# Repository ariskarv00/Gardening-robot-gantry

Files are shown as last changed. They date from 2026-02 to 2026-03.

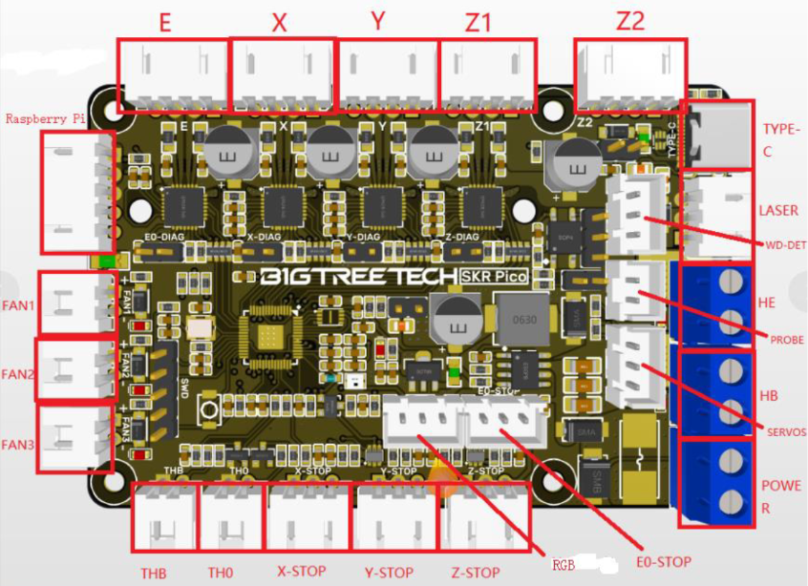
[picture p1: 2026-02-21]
electronics/SKR pico schematics.png

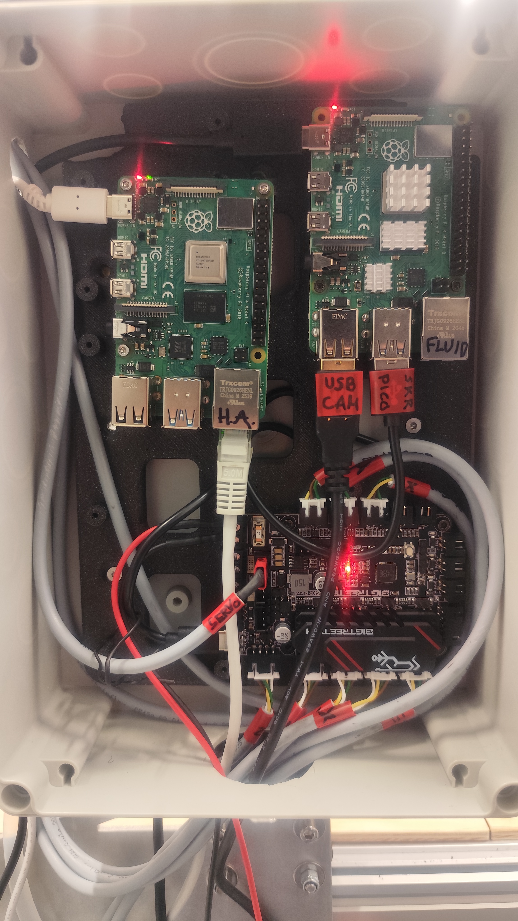
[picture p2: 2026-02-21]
electronics/IMG_20260129_140712.jpg

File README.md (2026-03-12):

# Gardening Robot Gantry (Danish Technical University - Skylab)

Modular Cartesian gardening robot inspired by the FarmBot Genesis, designed and built at DTU Skylab as a platform for student projects, course integration, and future startup exploration.

DTU Skylab - Gardening Robot - Demonstration: https://studio.youtube.com/video/Ki-VsF5vse0/edit

DTU Skylab - Gardening Robot - Seeding Sequence Testing: https://www.youtube.com/watch?v=myrVL9h8MHA 

DTU Skylab - Gardening Robot - Basic movements demo: https://www.youtube.com/watch?v=C3N4Af2INCI

Farmbot: https://farm.bot/

Farmbot Genesis Documentation: https://genesis.farm.bot/v1.8/assembly/intro

\## Features

\- 4×4 modular pot grid with laser‑cut wooden puzzle frame and 3D‑printed connectors  

\- Aluminum‑extrusion CNC gantry with V‑slot X/Z and leadscrew Y‑axis  

\- Toolhead with seed dispenser, watering nozzle, peristaltic pump, and USB camera  

\- Fully automated sequence: drill hole → drop seed → cover → water  

\- Calibrated peristaltic pump with ml‑per‑mm factor  

\- Browser‑based control via Klipper + Fluidd and automation via Home Assistant  

\## Repository layout

\- `hardware/` – CAD models (.f3d), .DXF for wooden puzzle grid, and BOM (.xlsx) 

\- `electronics/` – Schematics and wiring diagrams, pictures of connections 

\- `firmware/klipper/` – `printer.cfg` and pictures of Fluidd UI 

\- `documentation/` – Build guide, user guide, and notes for future improvements  

\- `pictures/` – Pictures of the assembly and 3D models

\## Hardware overview

\- Aluminum extrusion frame and V‑slot linear motion  

\- Custom metal parts (milled, lathed, laser‑/waterjet‑cut, hand‑finished)  

\- Laser‑cut 16‑pot grid mounted on 3D‑printed legs and extrusion supports  

\- NEMA17 steppers, micro servo for seed dispenser, peristaltic pump, mechanical endstops  

\## Electronics \& software

\- 1× Raspberry Pi running Klipper + Fluidd with BTT SKR Pico motion controller  

\- 1× Raspberry Pi running Home Assistant for automation  

\- Custom wiring with JST connectors and soldered harnesses  

\- Klipper configuration for axis calibration, safe homing, travel limits, and planting/watering macros  

\## Documentation

See `documentation/` for:

\- Step‑by‑step build instructions - Also follow Farmbot's Genesis documentation: https://genesis.farm.bot/v1.8/assembly/intro

\- Basic operation and maintenance  

\- Ideas and guidelines for future extensions (vision, sensors, new tools)

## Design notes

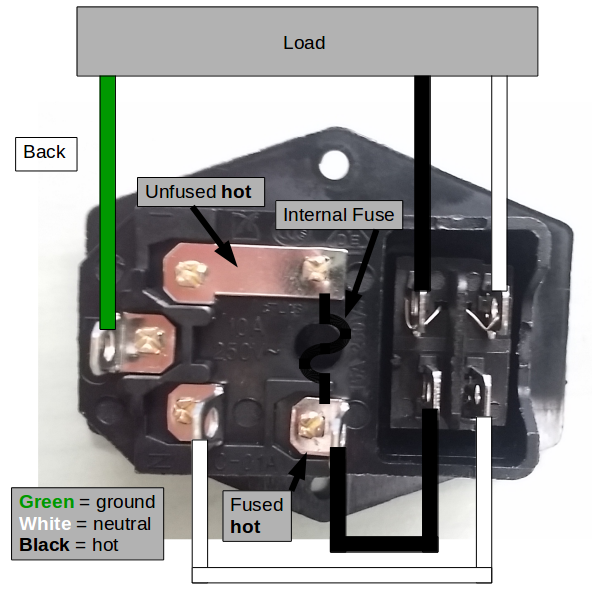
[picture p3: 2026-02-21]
electronics/IEC switch connection.webp

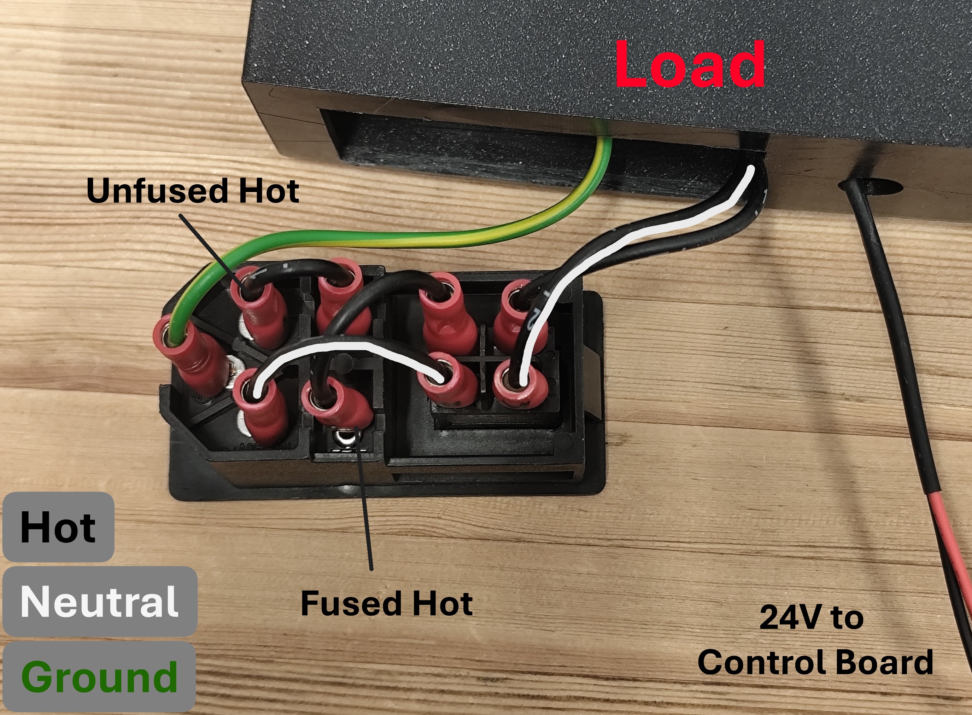
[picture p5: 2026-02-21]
electronics/Fuse Switch.jpg

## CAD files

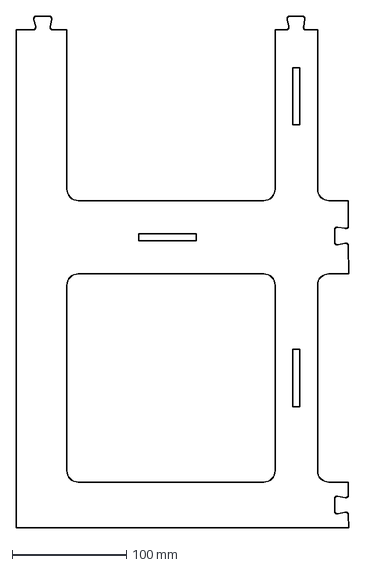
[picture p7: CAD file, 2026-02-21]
hardware/DXF Files for Wooden Puzzle-Grid/3.dxf
290.1 x 447.1 mm

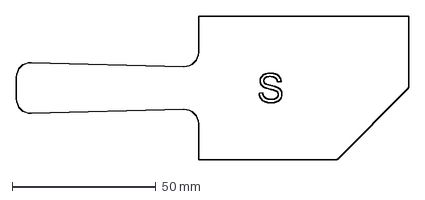
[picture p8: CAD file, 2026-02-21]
hardware/DXF Files for Wooden Puzzle-Grid/Short 2.dxf
136.3 x 50.0 mm

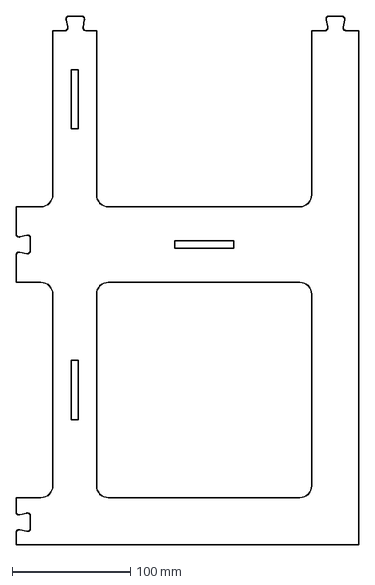
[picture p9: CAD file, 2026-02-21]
hardware/DXF Files for Wooden Puzzle-Grid/1.dxf
290.1 x 447.2 mm

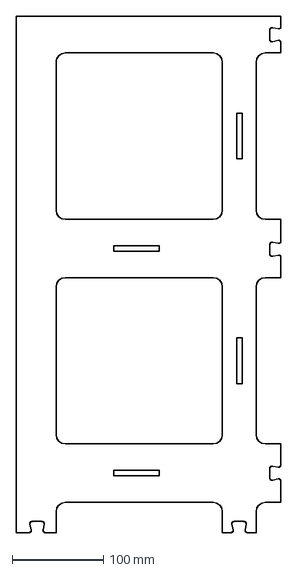
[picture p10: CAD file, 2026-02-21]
hardware/DXF Files for Wooden Puzzle-Grid/6.dxf
290.1 x 565.0 mm

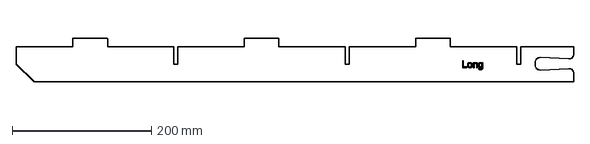
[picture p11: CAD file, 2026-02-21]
hardware/DXF Files for Wooden Puzzle-Grid/Long 1.dxf
800.0 x 62.0 mm

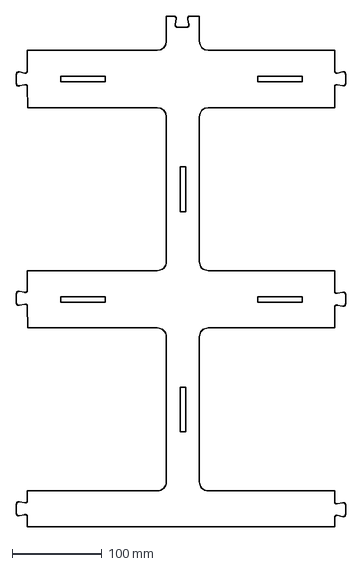
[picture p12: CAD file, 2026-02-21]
hardware/DXF Files for Wooden Puzzle-Grid/2.dxf
367.4 x 570.0 mm

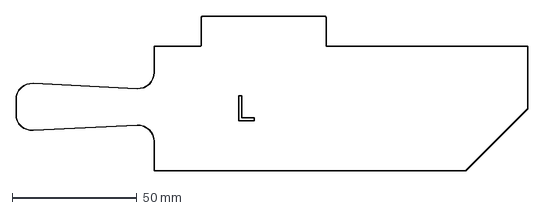
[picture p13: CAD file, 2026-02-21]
hardware/DXF Files for Wooden Puzzle-Grid/Long 2.dxf
205.4 x 62.0 mm

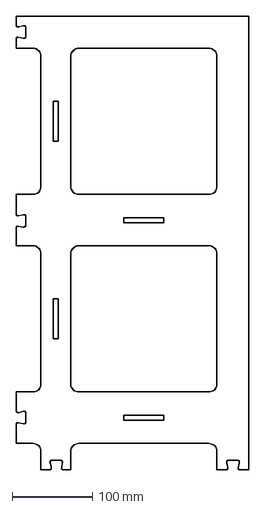
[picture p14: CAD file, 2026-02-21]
hardware/DXF Files for Wooden Puzzle-Grid/4.dxf
290.1 x 565.0 mm

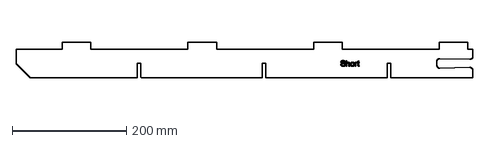
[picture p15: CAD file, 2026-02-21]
hardware/DXF Files for Wooden Puzzle-Grid/Short 1.dxf
800.0 x 62.0 mm

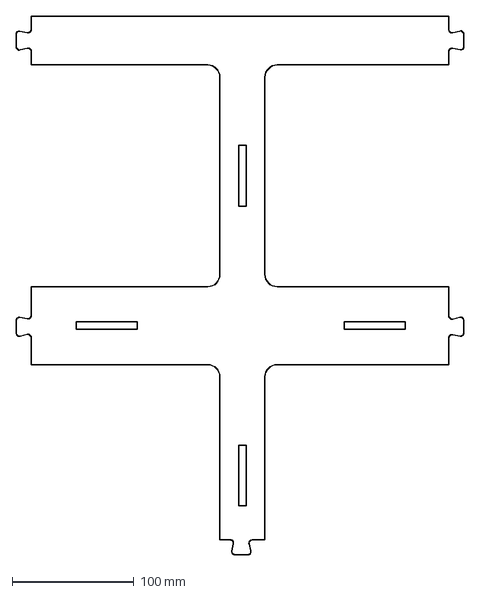
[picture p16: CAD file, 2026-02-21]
hardware/DXF Files for Wooden Puzzle-Grid/5.dxf
367.2 x 442.1 mm

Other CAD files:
hardware/Parametric Cable Chain.f3d
hardware/Parametric Peristaltic Pump with Mount.f3d

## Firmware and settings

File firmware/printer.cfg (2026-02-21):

[include fluidd.cfg]
[mcu]
 serial: /dev/serial/by-id/usb-Klipper_rp2040_45503571290C9388-if00

[virtual_sdcard]
path: /home/pi/printer_data/gcodes
on_error_gcode: CANCEL_PRINT

[printer]
kinematics: cartesian
max_velocity: 85    ;max velocity 85 for Z-axis not to malfuction
max_accel: 400
max_z_velocity: 80
max_z_accel: 400

[homing_override]
axes: yxz
gcode:
    G28 Y # Y axis first for safety (vertical)
    G28 X # home X axis
    G28 Z # home Z axis
    
[gcode_arcs]
resolution: 1.0
#   An arc will be split into segments. Each segment's length will
#   equal the resolution in mm set above. Lower values will produce a
#   finer arc, but also more work for your machine. Arcs smaller than
#   the configured value will become straight lines. The default is
#   1mm.

[stepper_x]
step_pin: gpio11
dir_pin: !gpio10
enable_pin: !gpio12
microsteps: 16
rotation_distance: 20   # CALIBRATION FORMULA: RD'=RD*(Lmeasured/Lreal),  
endstop_pin: !gpio4        # Lmeasured= the 'wrong' one, Lreal= real measured
position_endstop: 0
position_max: 730
homing_speed: 65
second_homing_speed: 10

[tmc2209 stepper_x]
uart_pin: gpio9
tx_pin: gpio8
uart_address: 0
run_current: 0.8
hold_current: 0.6
stealthchop_threshold: 999999

[stepper_y]
step_pin: gpio6
dir_pin: !gpio5
enable_pin: !gpio7
microsteps: 16
rotation_distance: 3.8
endstop_pin: !gpio3
position_endstop: 0
position_max: 315  
homing_speed: 35  
second_homing_speed: 10 


[tmc2209 stepper_y]
uart_pin: gpio9
tx_pin: gpio8
uart_address: 2
run_current: 0.8
hold_current: 0.6
stealthchop_threshold: 999999
diag_pin: ^gpio3
driver_SGTHRS: 100

[stepper_z]
step_pin: gpio19
dir_pin: gpio28
enable_pin: !gpio2
microsteps: 16
rotation_distance: 20
endstop_pin: !gpio25
position_endstop: 0
position_min: -2.0
position_max: 730
homing_speed: 55
second_homing_speed: 10
homing_retract_dist: 5.0


[tmc2209 stepper_z]
uart_pin: gpio9
tx_pin: gpio8
uart_address: 1
run_current: 1.2
hold_current: 0.6
stealthchop_threshold: 999999

[extruder]
step_pin: gpio14
dir_pin: !gpio13
enable_pin: !gpio15
microsteps: 16
rotation_distance: 14 ;So that mm translates into mL
nozzle_diameter: 0.4
filament_diameter: 1.75
heater_pin: gpio23
sensor_type: EPCOS 100K B57560G104F
sensor_pin: gpio27
control: pid
pid_Kp: 22.2
pid_Ki: 1.08
pid_Kd: 114
min_temp: -25 
max_temp: 20
max_extrude_cross_section:2
min_extrude_temp:-25
max_extrude_only_distance: 50000.0   ; or some value larger than the longest pump cycle you expect
max_extrude_cross_section: 10000.0      ; or even higher if you need greater flow
max_extrude_only_velocity: 600.0    # mm/s  — start conservative for a pump
max_extrude_only_accel: 2000.0    # mm/s^2 — reasonable starting accel

[tmc2209 extruder]
uart_pin: gpio9
tx_pin: gpio8
uart_address: 3
run_current: 1.00
hold_current: 0.800
stealthchop_threshold: 0

[gcode_macro MOVE_TO_PUMP_CALIBRATION_POSITION_B2]
description: Go to position and down to calibrate pump
gcode:
    G90
    G0 Y0 F4000
    G0 X287 Z230 F9999
    G0 Y300 F4000

[gcode_macro WATER_PLANT_CENTER]
description: Dispense water using peristaltic pump (slow start)
gcode:
    {% set volume = params.VOLUME|default(100)|float %}
    {% set flow_rate = params.FLOW_RATE|default(2000)|float %}

    ; CALIBRATION: mm of E per ml
    {% set e_per_ml = 4.1 %}
    {% set e_total = volume * e_per_ml %}

    {% set e_start = 10.0 %}
    {% set e_start = e_start if e_start < e_total else e_total %}
    {% set e_rest = e_total - e_start %}

    M83                     ; Relative extruder mode

    ; Slow start (anti-stall)
    G1 E{e_start} F500

    ; Normal watering
    {% if e_rest > 0 %}
        G1 E{e_rest} F{flow_rate}
    {% endif %}

    G4 P1000                ; Let flow finish
    M82                     ; Absolute extruder mode


[gcode_macro WATER_AFTER_PLANTING]
description: Water seed after planting with slow start then fast flow
gcode:
    ; --- Move nozzle to watering height ---
    G90
    G0 Y200 F4000

    ; --- Slow priming phase (5 ml at low speed) ---
    {% set slow_volume = 5 %}
    {% set slow_flow = 500 %}
    {% set slow_e = slow_volume * 2 %}   ; CALIBRATED: mm per ml

    M83
    G1 E{slow_e} F{slow_flow}
    G4 P500

    ; --- Main watering phase (55 ml at high speed) ---
    {% set fast_volume = 55 %}
    {% set fast_flow = 3000 %}
    {% set fast_e = fast_volume * 2 %}

    G1 E{fast_e} F{fast_flow}
    G4 P1000
    M82


[servo Seeder]
pin: gpio29          # g-code command  SET_SERVO SERVO=Seeder ANGLE=180
maximum_servo_angle: 180
#   The maximum angle (in degrees) that this servo can be set to. The
#   default is 180 degrees.
#initial_angle:
#   Initial angle (in degrees) to set the servo to. The default is to
#   not send any signal at startup.

[gcode_macro DROP_SEED]
description: Drop seed at current position 
gcode:
    G4 P500  
      SET_SERVO SERVO=Seeder ANGLE=180  ; Rotate to release seed
      G4 P500                    ; Brief pause for seed to drop
      SET_SERVO SERVO=Seeder ANGLE=0    ; Return to closed position
    G4 P500  


[gcode_macro DROP_SEED_WITH_VIBRATION]
description: Drop seed at current position with vibration to free stuck pellets
gcode:
    # Small delay before starting
    G4 P500  

    ################################################################
    # 1) PRE-DROP VIBRATION AROUND CLOSED POSITION (0°)
    ################################################################
    
    SET_SERVO SERVO=Seeder ANGLE=70
    G4 P100                    ; Brief pause
    SET_SERVO SERVO=Seeder ANGLE=0
    G4 P100                    ; Brief pause
    SET_SERVO SERVO=Seeder ANGLE=70
    G4 P100                    ; Brief pause
    SET_SERVO SERVO=Seeder ANGLE=0
    G4 P100                    ; Brief pause
    SET_SERVO SERVO=Seeder ANGLE=70
    G4 P100                    ; Brief pause
    SET_SERVO SERVO=Seeder ANGLE=0
    G4 P100                    ; Brief pause
    SET_SERVO SERVO=Seeder ANGLE=70
    G4 P100                    ; Brief pause
    SET_SERVO SERVO=Seeder ANGLE=0
    G4 P50                    ; Brief pause
    SET_SERVO SERVO=Seeder ANGLE=70
    G4 P100                    ; Brief pause
    SET_SERVO SERVO=Seeder ANGLE=0
    G4 P100                    ; Brief pause
    SET_SERVO SERVO=Seeder ANGLE=70
    G4 P100                    ; Brief pause
    SET_SERVO SERVO=Seeder ANGLE=0
    G4 P100                    ; Brief pause

    SET_SERVO SERVO=Seeder ANGLE=180      ; Rotate to release seed
    

    G4 P800    ; brief pause for seed to drop

    SET_SERVO SERVO=Seeder ANGLE=0    ; Return to closed position


    G4 P500    ; end delay

[gcode_macro PLANT_SEED_WITH_HOLE_FIRST]
description: Plant seed at current position, making a hole first
gcode:
    G91
    G0 X10 F4000               ; Move X above the hole
    G90

    G0 Y312 F9999              ; Move down to make a hole
    G0 Y285 F4000              ; Move up begin seed drop sequence
    
    G91                        ; 
    G0 X-10 F4000               ; Move X above the hole
    G90
    
    G4 P500  
    SET_SERVO SERVO=Seeder ANGLE=180  ; Rotate to release seed
    G4 P500                           ; Brief pause for seed to drop
    SET_SERVO SERVO=Seeder ANGLE=0    ; Return to closed position
    G4 P500 

    G91
    G0 X-10 F4000                 ; Move back to begin covering the hole
    G0 Y25 F4000                ; Start covering the hole   
    G0 X10 F4000                 ; Cover the hole
    G90   

    G0 Y0 F4000               ; Move back up
    

[gcode_macro SQUARE_MOVEMENT_AROUND_CENTER]
description: Centered square in XZ around current position. Goes to Y150 first.
gcode:
    ; D = side length of square (your "diameter")
    {% set d = params.D|default(50)|float %}
    {% set h = d / 2.0 %}
    {% set neg_h = -h %}
    {% set neg_d = -d %}
    {% set f = params.F|default(5000)|float %}

    ; Go to watering height first (absolute)
    G90
    G0 Y150 F4000

    ; Now do the square around the start point in relative mode
    G91

    ; Your exact pattern, but parametric:
    ; z +h
    G0 Z{h} F{f}
    ; x +h
    G0 X{h} F{f}
    ; z -d
    G0 Z{neg_d} F{f}
    ; x -d
    G0 X{neg_d} F{f}
    ; z +d
    G0 Z{d} F{f}
    ; x +h
    G0 X{h} F{f}
    ; z -h  (back to center)
    G0 Z{neg_h} F{f}

    G90
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

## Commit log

2026-02-21 Add hardware, electronics, firmware, pics and docs
    [1.dxf, 2.dxf, 3.dxf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]
2026-02-21 CAD models (.f3d), .DXF for wooden puzzle grid, and BOM (.xlsx)
    [1.dxf, 2.dxf, 3.dxf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]
2026-02-21 Pictures of the assembly and 3D models
2026-02-21 `printer.cfg` and pictures of Fluidd UI
2026-02-21 Schematics and wiring diagrams, pictures of connections
2026-03-12 Complete documentation PDF, assembly, part selection, manual etc.
